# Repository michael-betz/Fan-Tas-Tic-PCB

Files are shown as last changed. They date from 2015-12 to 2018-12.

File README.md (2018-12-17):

# Fan-Tas-Tic-PCB
Kicad files for the Fan-Tas-Tic pinball controller.
No tiny SMD components, can be easily assembled by hand.
Designed for the milling machine (2 sided but no real vias, using through hole components instead).

# Mainboard

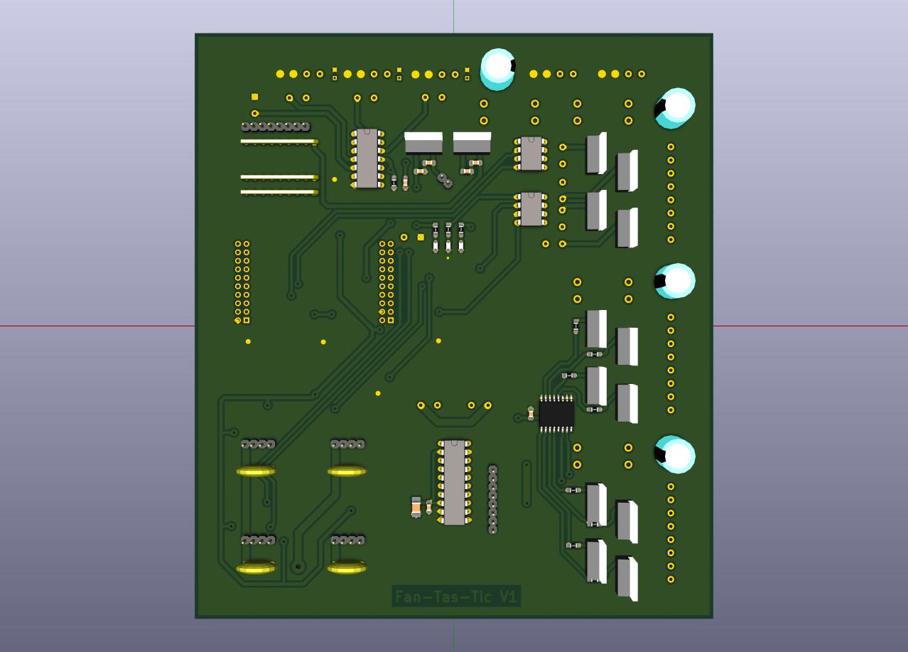
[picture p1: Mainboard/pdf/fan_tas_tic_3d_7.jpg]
3D view of the Mainboard


[Schematic](https://raw.githubusercontent.com/yetifrisstlama/Fan-Tas-Tic-PCB/master/Mainboard/pdf/fan_tas_tic.pdf)

 * Based on TM4C123GXL evaluation board
 * 8 x 8 Switch matrix inputs (Operating on 12 V)
 * 12 x on-board open drain drivers for solenoids
 * 4 of them can do hardware PWM (> 100 kHz)
 * Fused in groups of 4
 * 4 x I2C channels for hardware extension boards.
   In- / Outputs can be easily and cheaply added with PCF8574 I2C GPIO extenders
 * 3 x SPI channels for running WS2811 / WS2812 LED strings.
   Up to 1024 LEDs / channel.
 * USB virtual serial connection to host PC (or Raspberry PI)
 * 5 V can come from USB or from external 24 V input (Set JP1)
 * SMD resistors / capacitors = 0805
 * Switch matrix driver:
   [TPIC6B595](http://www.ti.com/lit/ds/symlink/tpic6b595.pdf) (eBay)
 * GPIO extender:
   [PCF8574](http://www.ti.com/lit/ds/symlink/pcf8574.pdf) (eBay)
 * Dual power mosfet driver:
   [UCC27524](http://www.ti.com/lit/ds/symlink/ucc27524.pdf)
 * Power mosfets:
   [IRL640](http://www.vishay.com/docs/91305/91305.pdf)
 * Signal mosfet for I2C level conversion:
   [BSS138](https://www.fairchildsemi.com/datasheets/BS/BSS138.pdf)
 * 8 pin solenoid and 4 pin power connectors:
   [HT396](https://www.google.com/search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,ssl&ei=fLGbVpy5GMX4apzWrtgK)
 * 8 pin switch-matrix and 4 pin I2C connectors:
   [KF2510](https://www.google.com/search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,ssl&ei=HrKbVpHDFoKua7iAu-AK)

## Status
The current version of the Mainboard PCB (06/2016) has been tested and worked as expected without any major problems. See also the [development blog](http://yetifrisstlama.blogspot.fr/). For the next revision, these (minor) issues will be fixed:
 * `Debug` USB connector on the Tiva board interferes with the I2C connectors on the mainboard. These will be moved.
 * An `Interlock` Relay will be introduced on the 24 V supply line for the solenoid drivers. This is needed as the I2C port extenders have by default all outputs active before beeing initialized (which only happens a few 10 ms after power up). Furthermore, if the firmware crashes, has I2C connection issues or locks up, it can cut the power from an fault-handler.
 * Freewheeling diodes _MUST_ be Schottky diodes and will be included on the PCB next to the mosfets (not on the solenoids!) for accetable EMI performance. This has been found experimentally (http://yetifrisstlama.blogspot.fr/).
 * More footprints for decoupling caps will be included

# Input extension board
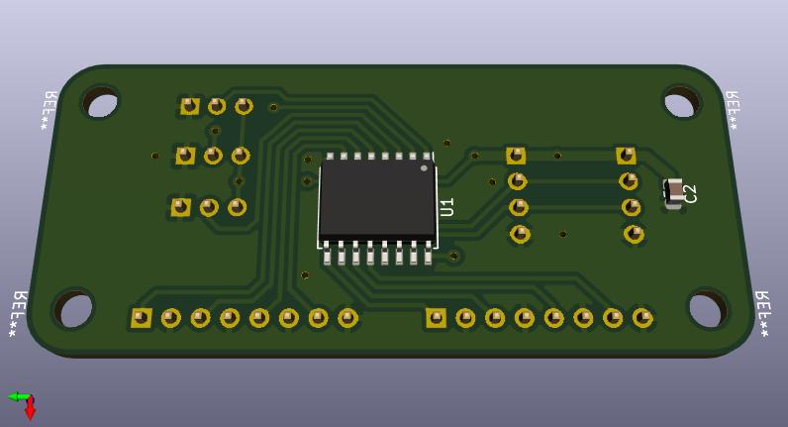
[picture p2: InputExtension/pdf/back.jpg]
3D view of the input extension board


[Schematic](https://raw.githubusercontent.com/yetifrisstlama/Fan-Tas-Tic-PCB/master/InputExtension/pdf/InputExtension.pdf)

 * 8 shiny new input channels for your pinball machine
 * as simple and cheap as it gets
 * read out a zooming 1000 times a second

## Status
[Built, tested, works as expected :)](https://yetifrisstlama.github.io/fan-tas-tic-score-reels/)

# Output extension board
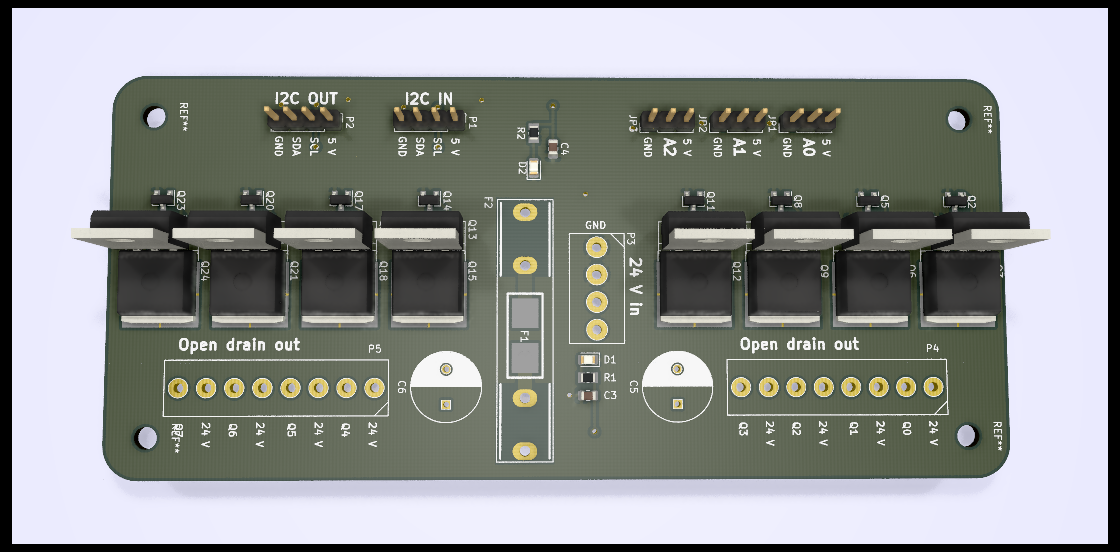
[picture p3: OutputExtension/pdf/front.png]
3D view of the output extension board


[Schematic](https://raw.githubusercontent.com/yetifrisstlama/Fan-Tas-Tic-PCB/master/OutputExtension/pdf/OutputExtension.pdf)

 * 8 beefy open drain outputs to rock some solenoids
 * BYOM! Bring your own mosfets ... supports TO-220, TO-263 and SOT23 footprints
 * Fused, to keep the magic smoke in
 * Also drives motors, LED strings, LED floodlights ...

## Status
Built, tested, no issues found. Drives my score reels like a charm.

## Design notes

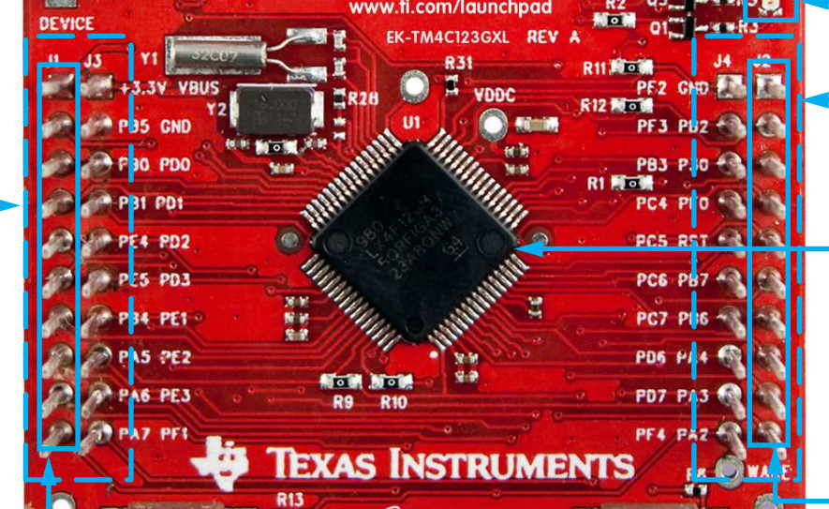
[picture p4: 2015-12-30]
Mainboard/TIVIA_Board.jpg

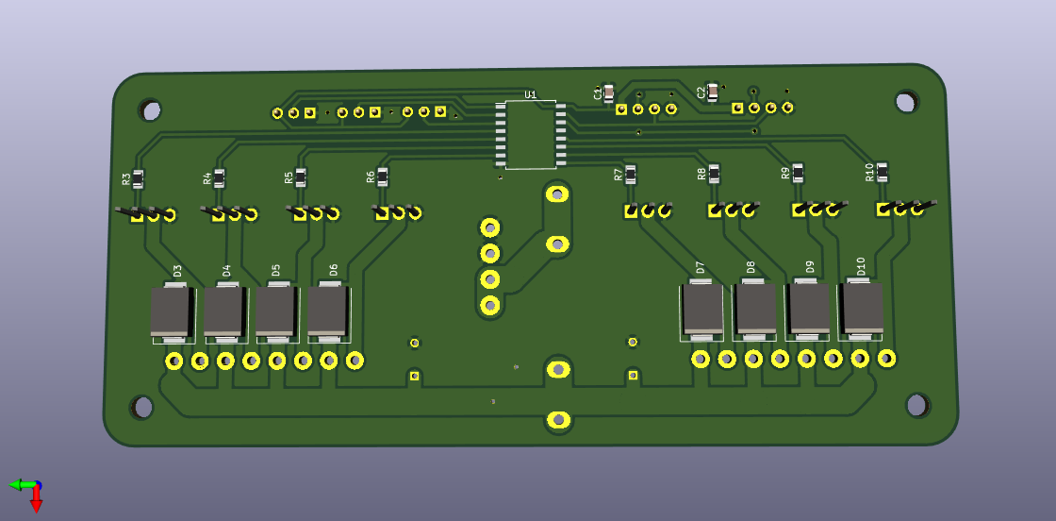
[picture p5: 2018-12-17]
OutputExtension/pdf/back.png

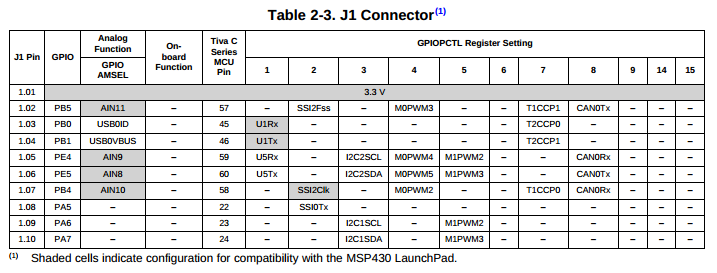
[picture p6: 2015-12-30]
Mainboard/TivaJ1.png

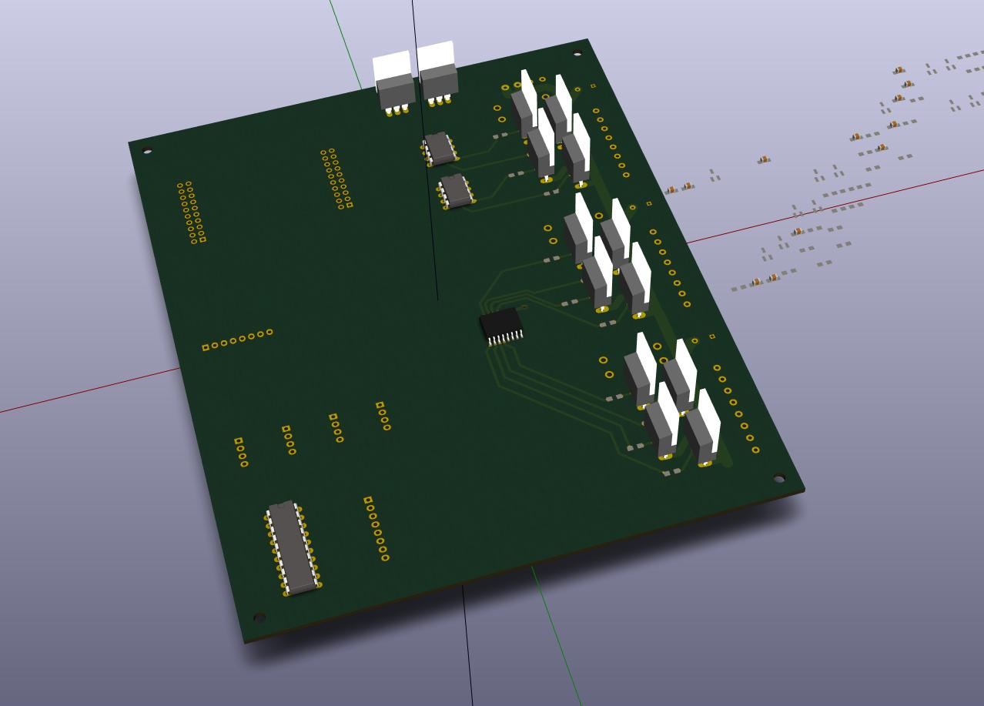
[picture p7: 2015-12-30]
Mainboard/pdf/fan_tas_tic_3d_2.jpg

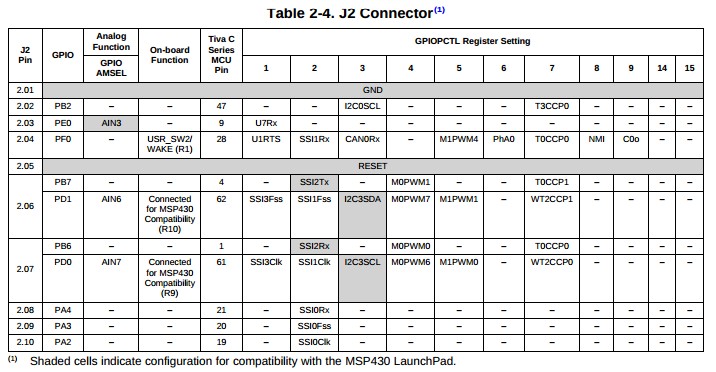
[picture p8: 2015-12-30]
Mainboard/TivaJ2.png

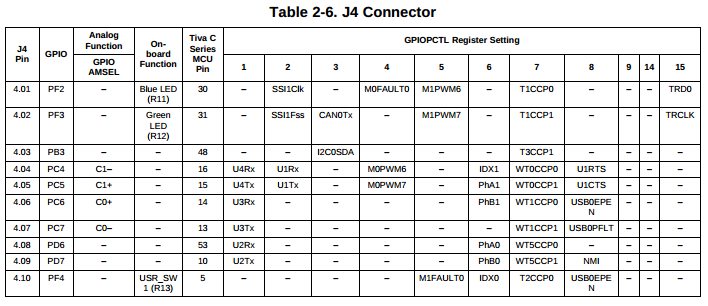
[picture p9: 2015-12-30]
Mainboard/TivaJ4.png

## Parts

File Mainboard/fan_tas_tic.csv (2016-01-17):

Reference | Value | Footprint | Datasheet
P6 | CONN_01X08 | Pin_Headers:Pin_Header_Straight_1x08
P8 | CONN_01X08 | Pin_Headers:Pin_Header_Straight_1x08
P7 | CONN_01X08 | my_foots:HT396_8
F1 | FUSE | Fuse_Holders_and_Fuses:Fuseholder5x20_horiz_open_universal_Type-III
C12 | 470 uF | Capacitors_ThroughHole:C_Radial_D10_L16_P5
U3 | UCC27524 | Housings_DIP:DIP-8_W7.62mm_LongPads
U4 | UCC27524 | Housings_DIP:DIP-8_W7.62mm_LongPads
C9 | 300nF | Capacitors_SMD:C_1812_HandSoldering
C10 | 300nF | Capacitors_SMD:C_1812_HandSoldering
R2 | 47R | Resistors_ThroughHole:Resistor_Vertical_RM5mm
R1 | 47R | Resistors_ThroughHole:Resistor_Vertical_RM5mm
R5 | 47R | Resistors_ThroughHole:Resistor_Vertical_RM5mm
R14 | 47R | Resistors_ThroughHole:Resistor_Vertical_RM5mm
C1 | 330n | Capacitors_SMD:C_0805_HandSoldering
C3 | 100n | Capacitors_SMD:C_0805_HandSoldering
P1 | CONN_01X04 | my_foots:HT396_4
C2 | 330n | Capacitors_SMD:C_0805_HandSoldering
P9 | CONN_01X08 | my_foots:HT396_8
F2 | FUSE | Fuse_Holders_and_Fuses:Fuseholder5x20_horiz_open_universal_Type-III
C14 | 470 uF | Capacitors_ThroughHole:C_Radial_D10_L16_P5
P10 | CONN_01X08 | my_foots:HT396_8
F3 | FUSE | Fuse_Holders_and_Fuses:Fuseholder5x20_horiz_open_universal_Type-III
C15 | 470 uF | Capacitors_ThroughHole:C_Radial_D10_L16_P5
U6 | PCF8574 | Housings_SOIC:SOIC-16_7.5x10.3mm_Pitch1.27mm
C13 | 100n | Capacitors_SMD:C_0805_HandSoldering
P2 | CONN_01X04 | Pin_Headers:Pin_Header_Straight_1x04
C5 | 100n | Capacitors_ThroughHole:C_Disc_D12_P7.75
P3 | CONN_01X04 | Pin_Headers:Pin_Header_Straight_1x04
C6 | 100n | Capacitors_ThroughHole:C_Disc_D12_P7.75
P4 | CONN_01X04 | Pin_Headers:Pin_Header_Straight_1x04
C7 | 100n | Capacitors_ThroughHole:C_Disc_D12_P7.75
P5 | CONN_01X04 | Pin_Headers:Pin_Header_Straight_1x04
C8 | 100n | Capacitors_ThroughHole:C_Disc_D12_P7.75
R6 | 30k | Resistors_SMD:R_0805_HandSoldering
R7 | 30k | Resistors_SMD:R_0805_HandSoldering
R8 | 30k | Resistors_SMD:R_0805_HandSoldering
R9 | 30k | Resistors_SMD:R_0805_HandSoldering
R10 | 30k | Resistors_SMD:R_0805_HandSoldering
R11 | 30k | Resistors_SMD:R_0805_HandSoldering
R12 | 30k | Resistors_SMD:R_0805_HandSoldering
R13 | 30k | Resistors_SMD:R_0805_HandSoldering
C11 | 100n | Capacitors_SMD:C_0805_HandSoldering
R3 | 30k | Resistors_ThroughHole:Resistor_Vertical_RM5mm
R4 | 30k | Resistors_ThroughHole:Resistor_Vertical_RM5mm
U5 | TPIC6B595 | Housings_DIP:DIP-20_W7.62mm_LongPads
Q1 | IRL640 | TO_SOT_Packages_THT:TO-220_Neutral123_Vertical_LargePads
Q2 | IRL640 | TO_SOT_Packages_THT:TO-220_Neutral123_Vertical_LargePads
Q3 | IRL640 | TO_SOT_Packages_THT:TO-220_Neutral123_Vertical_LargePads
Q4 | IRL640 | TO_SOT_Packages_THT:TO-220_Neutral123_Vertical_LargePads
U2 | 7805 | my_foots:TO-220_Neutral123_Vertical_LargePads
U1 | 7812 | my_foots:TO-220_Neutral123_Vertical_LargePads
JP1 | Jumper_NO_Small | Pin_Headers:Pin_Header_Straight_1x02
C4 | 100n | Capacitors_SMD:C_0805_HandSoldering
P11 | CONN_01X04 | my_foots:HT396_4
C16 | 4700 uF | Capacitors_ThroughHole:C_Radial_D10_L16_P5
F4 | 10A | Fuse_Holders_and_Fuses:Fuseholder5x20_horiz_open_universal_Type-III
P13 | CONN_01X04 | my_foots:HT396_4
R51 | 470 | Resistors_ThroughHole:Resistor_Vertical_RM5mm
C18 | 300 nF | Capacitors_ThroughHole:C_Rect_L4_W2.5_P2.5
RR1 | RR8 | Resistors_ThroughHole:Resistor_Array_SIP8
RR2 | RR8 | Resistors_ThroughHole:Resistor_Array_SIP8
RR3 | RR8 | Resistors_ThroughHole:Resistor_Array_SIP8
C19 | 10u | Capacitors_SMD:C_1210_HandSoldering
P14 | CONN_01X04 | my_foots:HT396_4
R22 | 470 | Resistors_ThroughHole:Resistor_Vertical_RM5mm
C20 | 300 nF | Capacitors_ThroughHole:C_Rect_L4_W2.5_P2.5
P12 | CONN_01X04 | my_foots:HT396_4
R20 | 470 | Resistors_ThroughHole:Resistor_Vertical_RM5mm
C17 | 300 nF | Capacitors_ThroughHole:C_Rect_L4_W2.5_P2.5
C21 | 470n | Capacitors_SMD:C_0805_HandSoldering
C22 | 470n | Capacitors_SMD:C_0805_HandSoldering
D3 | LED | LEDs:LED-0805
R17 | 220 | Resistors_SMD:R_0805_HandSoldering
D2 | LED | LEDs:LED-0805
R16 | 820 | Resistors_SMD:R_0805_HandSoldering
D1 | LED | LEDs:LED-0805
R15 | 2200 | Resistors_SMD:R_0805_HandSoldering
U7 | 74HC04 | Housings_DIP:DIP-14_W7.62mm_LongPads
R18 | 4k7 | Resistors_ThroughHole:Resistor_Vertical_RM5mm
R19 | 4k7 | Resistors_ThroughHole:Resistor_Vertical_RM5mm
R21 | 4k7 | Resistors_SMD:R_0805_HandSoldering
C23 | 100nF | Capacitors_SMD:C_0805_HandSoldering
J1 | Ti_Booster_40 | my_foots:Tivia_Launch_Pad
R23 | 470R | Resistors_SMD:R_0805_HandSoldering
Q5 | IRL640 | TO_SOT_Packages_THT:TO-220_Neutral123_Vertical_LargePads
R24 | 470R | Resistors_SMD:R_0805_HandSoldering
Q6 | IRL640 | TO_SOT_Packages_THT:TO-220_Neutral123_Vertical_LargePads
R25 | 470R | Resistors_SMD:R_0805_HandSoldering
Q7 | IRL640 | TO_SOT_Packages_THT:TO-220_Neutral123_Vertical_LargePads
R26 | 470R | Resistors_SMD:R_0805_HandSoldering
Q8 | IRL640 | TO_SOT_Packages_THT:TO-220_Neutral123_Vertical_LargePads
R27 | 470R | Resistors_SMD:R_0805_HandSoldering
Q9 | IRL640 | TO_SOT_Packages_THT:TO-220_Neutral123_Vertical_LargePads
R28 | 470R | Resistors_SMD:R_0805_HandSoldering
Q10 | IRL640 | TO_SOT_Packages_THT:TO-220_Neutral123_Vertical_LargePads
R29 | 470R | Resistors_SMD:R_0805_HandSoldering
Q11 | IRL640 | TO_SOT_Packages_THT:TO-220_Neutral123_Vertical_LargePads
R30 | 470R | Resistors_SMD:R_0805_HandSoldering
Q12 | IRL640 | TO_SOT_Packages_THT:TO-220_Neutral123_Vertical_LargePads
R31 | 2k2 | Resistors_SMD:R_0805_HandSoldering
R32 | 2k2 | Resistors_SMD:R_0805_HandSoldering
R33 | 2k2 | Resistors_SMD:R_0805_HandSoldering
R34 | 2k2 | Resistors_SMD:R_0805_HandSoldering
Q13 | BSS138 | TO_SOT_Packages_SMD:SOT-23_Handsoldering
Q14 | BSS138 | TO_SOT_Packages_SMD:SOT-23_Handsoldering
R35 | 2k2 | Resistors_SMD:R_0805_HandSoldering
R36 | 2k2 | Resistors_SMD:R_0805_HandSoldering
R37 | 2k2 | Resistors_SMD:R_0805_HandSoldering
R38 | 2k2 | Resistors_SMD:R_0805_HandSoldering
Q15 | BSS138 | TO_SOT_Packages_SMD:SOT-23_Handsoldering
Q16 | BSS138 | TO_SOT_Packages_SMD:SOT-23_Handsoldering
R39 | 2k2 | Resistors_SMD:R_0805_HandSoldering
R40 | 2k2 | Resistors_SMD:R_0805_HandSoldering
R41 | 2k2 | Resistors_SMD:R_0805_HandSoldering
R42 | 2k2 | Resistors_SMD:R_0805_HandSoldering
Q17 | BSS138 | TO_SOT_Packages_SMD:SOT-23_Handsoldering
Q18 | BSS138 | TO_SOT_Packages_SMD:SOT-23_Handsoldering
R43 | 2k2 | Resistors_SMD:R_0805_HandSoldering
R44 | 2k2 | Resistors_SMD:R_0805_HandSoldering
R45 | 2k2 | Resistors_SMD:R_0805_HandSoldering
R46 | 2k2 | Resistors_SMD:R_0805_HandSoldering
Q19 | BSS138 | TO_SOT_Packages_SMD:SOT-23_Handsoldering
Q20 | BSS138 | TO_SOT_Packages_SMD:SOT-23_Handsoldering

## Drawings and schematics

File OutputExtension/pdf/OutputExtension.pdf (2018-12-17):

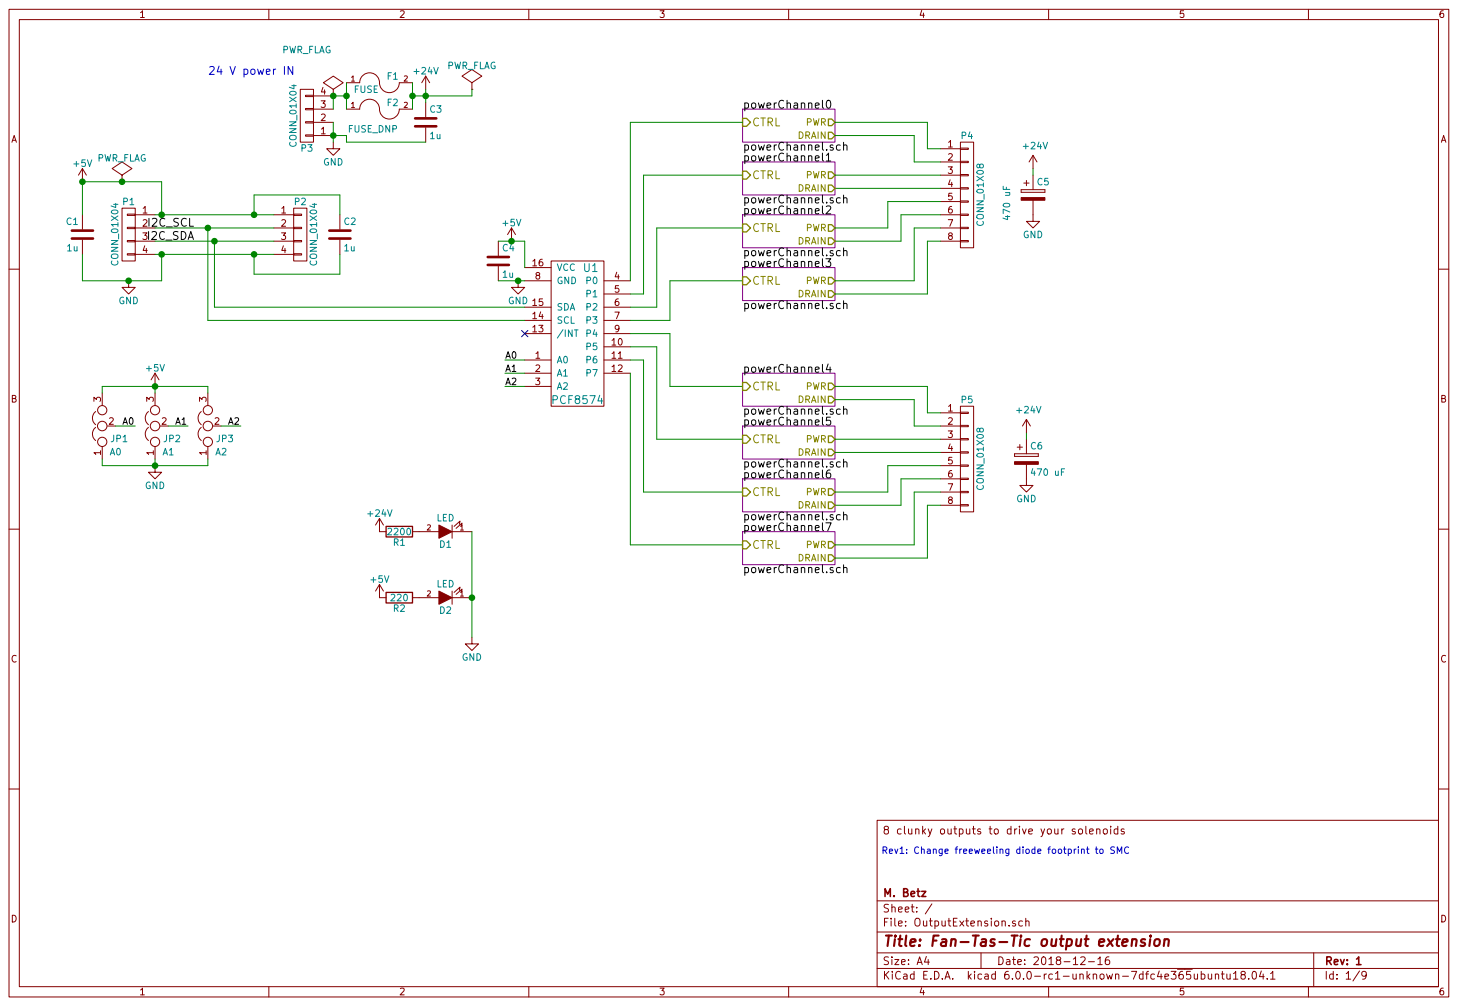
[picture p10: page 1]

File: OutputExtension.sch Sheet: / M. Betz 8 clunky outputs to drive your solenoids

Rev1: Change freeweeling diode footprint to SMC

Id: 1/9 Title: Fan-Tas-Tic output extension

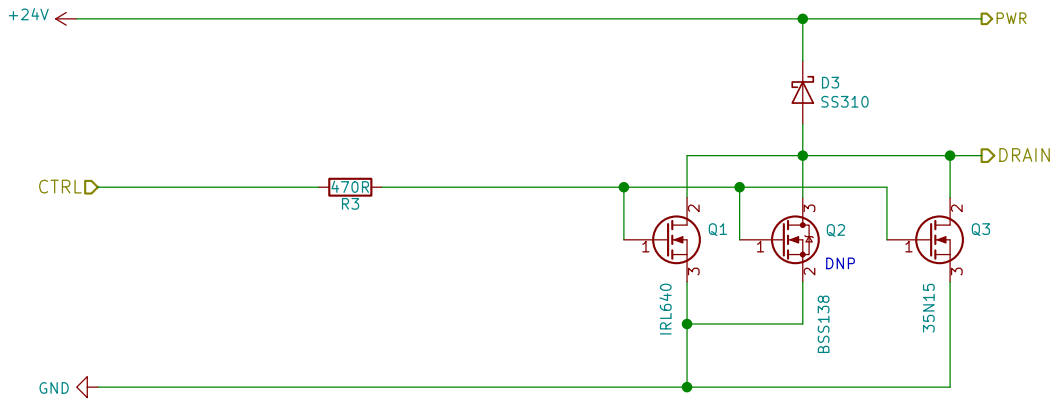
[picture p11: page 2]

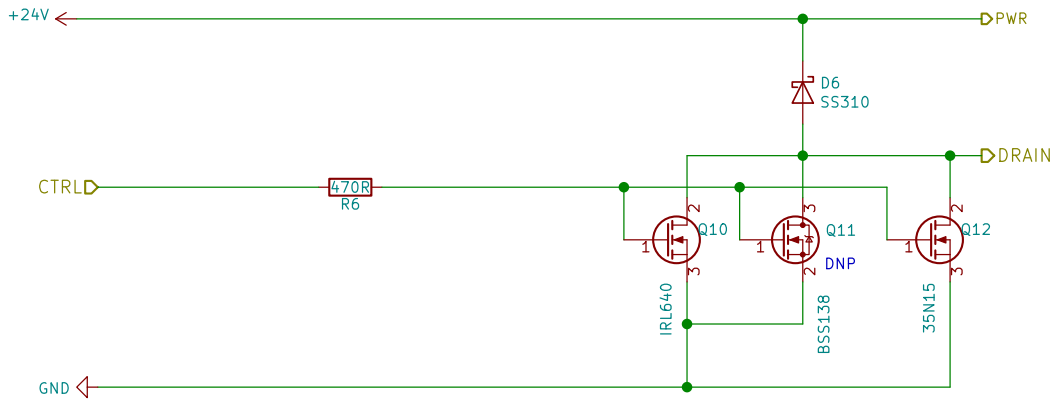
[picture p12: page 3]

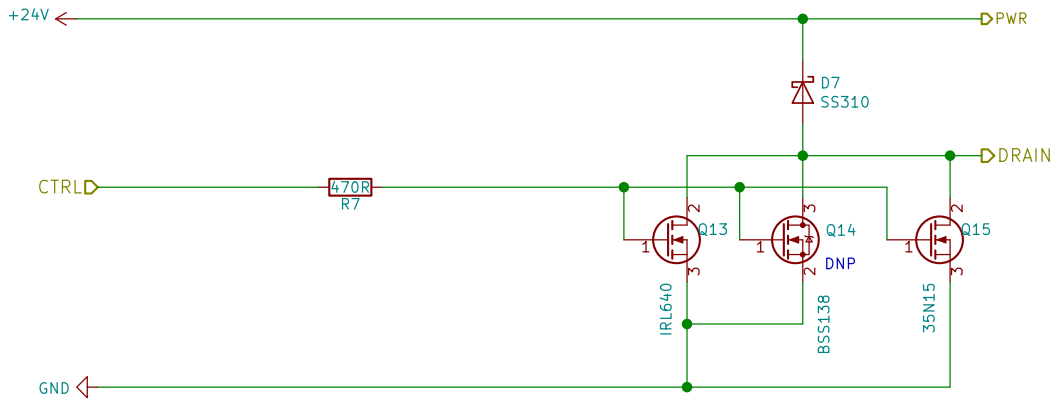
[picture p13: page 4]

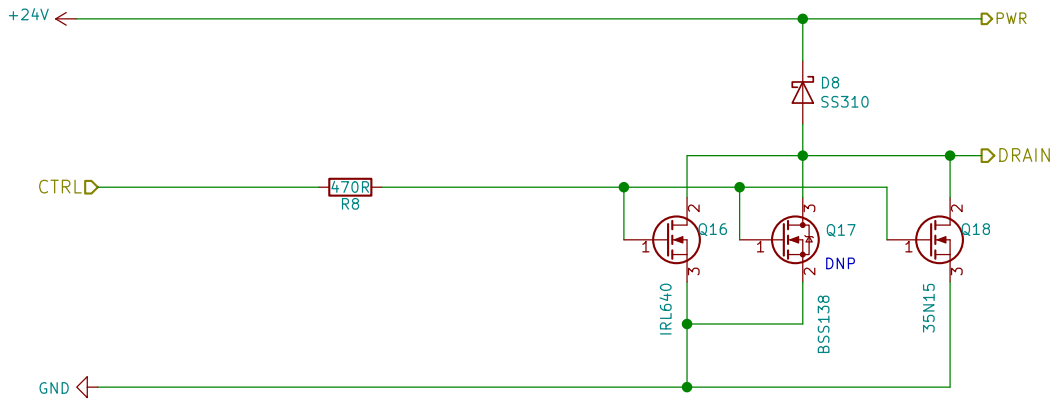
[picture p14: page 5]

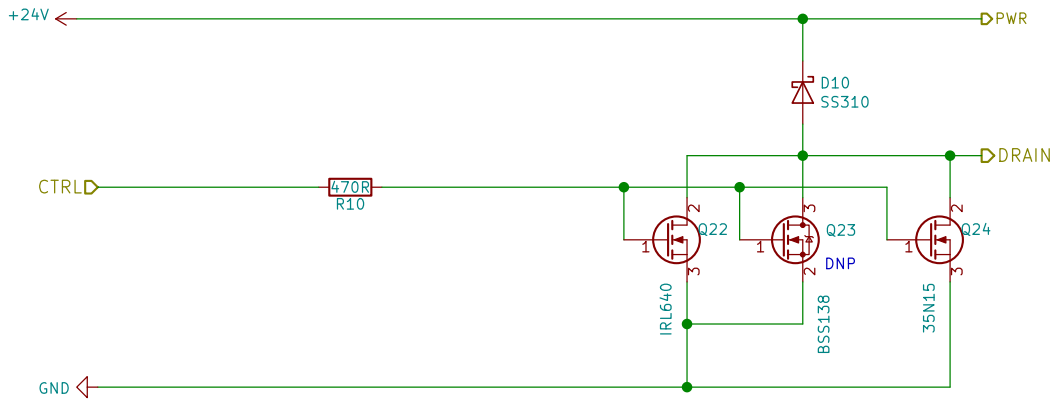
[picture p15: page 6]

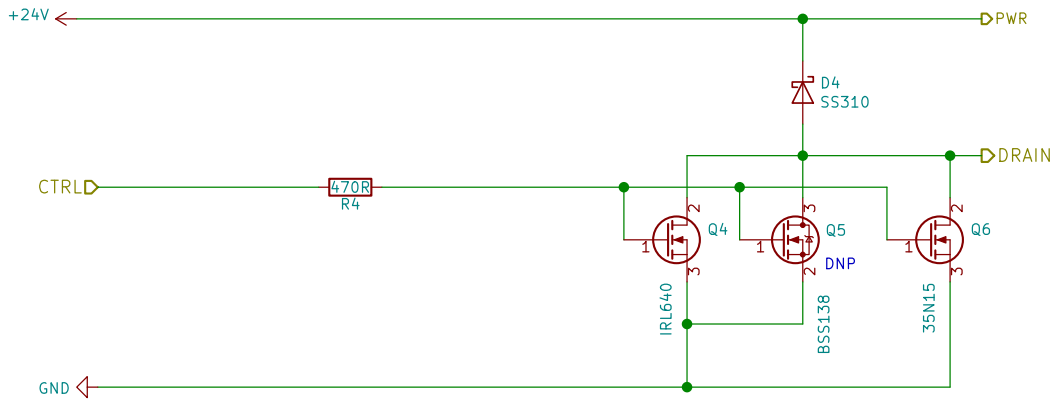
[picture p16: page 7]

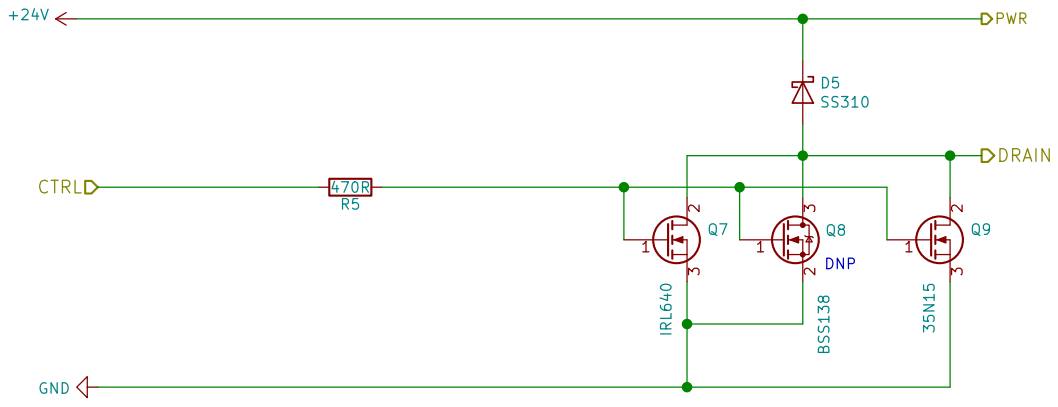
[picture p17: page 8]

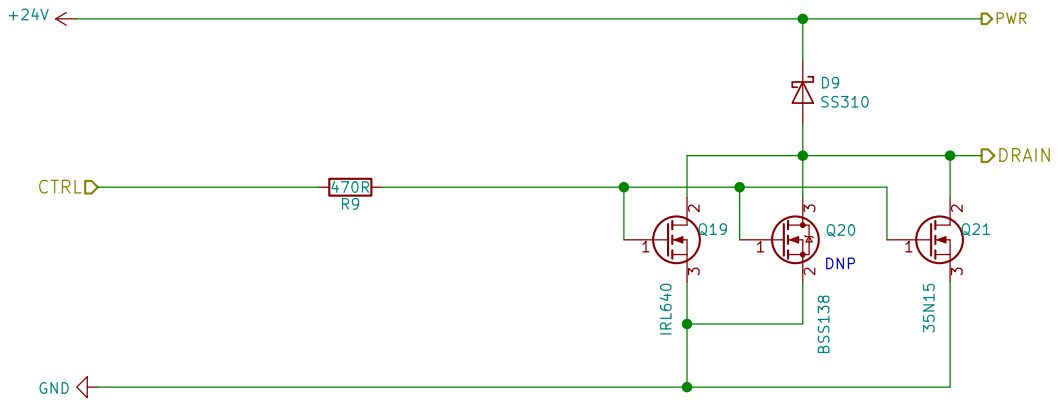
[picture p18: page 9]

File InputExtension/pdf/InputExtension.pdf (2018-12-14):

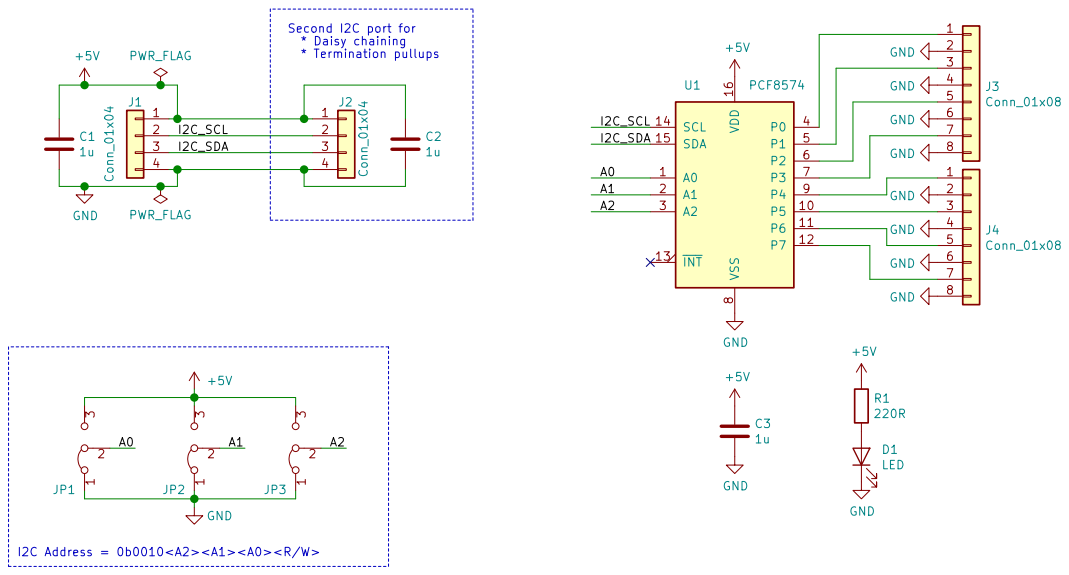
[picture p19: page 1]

J4Conn_01x08 GND GND GND GND GND GND GND GND

File: InputExtension.sch Sheet: / M. Betz 8 shiny new inputs for your pinball machine

Id: 1/1 Title: Fan-Tas-Tic input extension

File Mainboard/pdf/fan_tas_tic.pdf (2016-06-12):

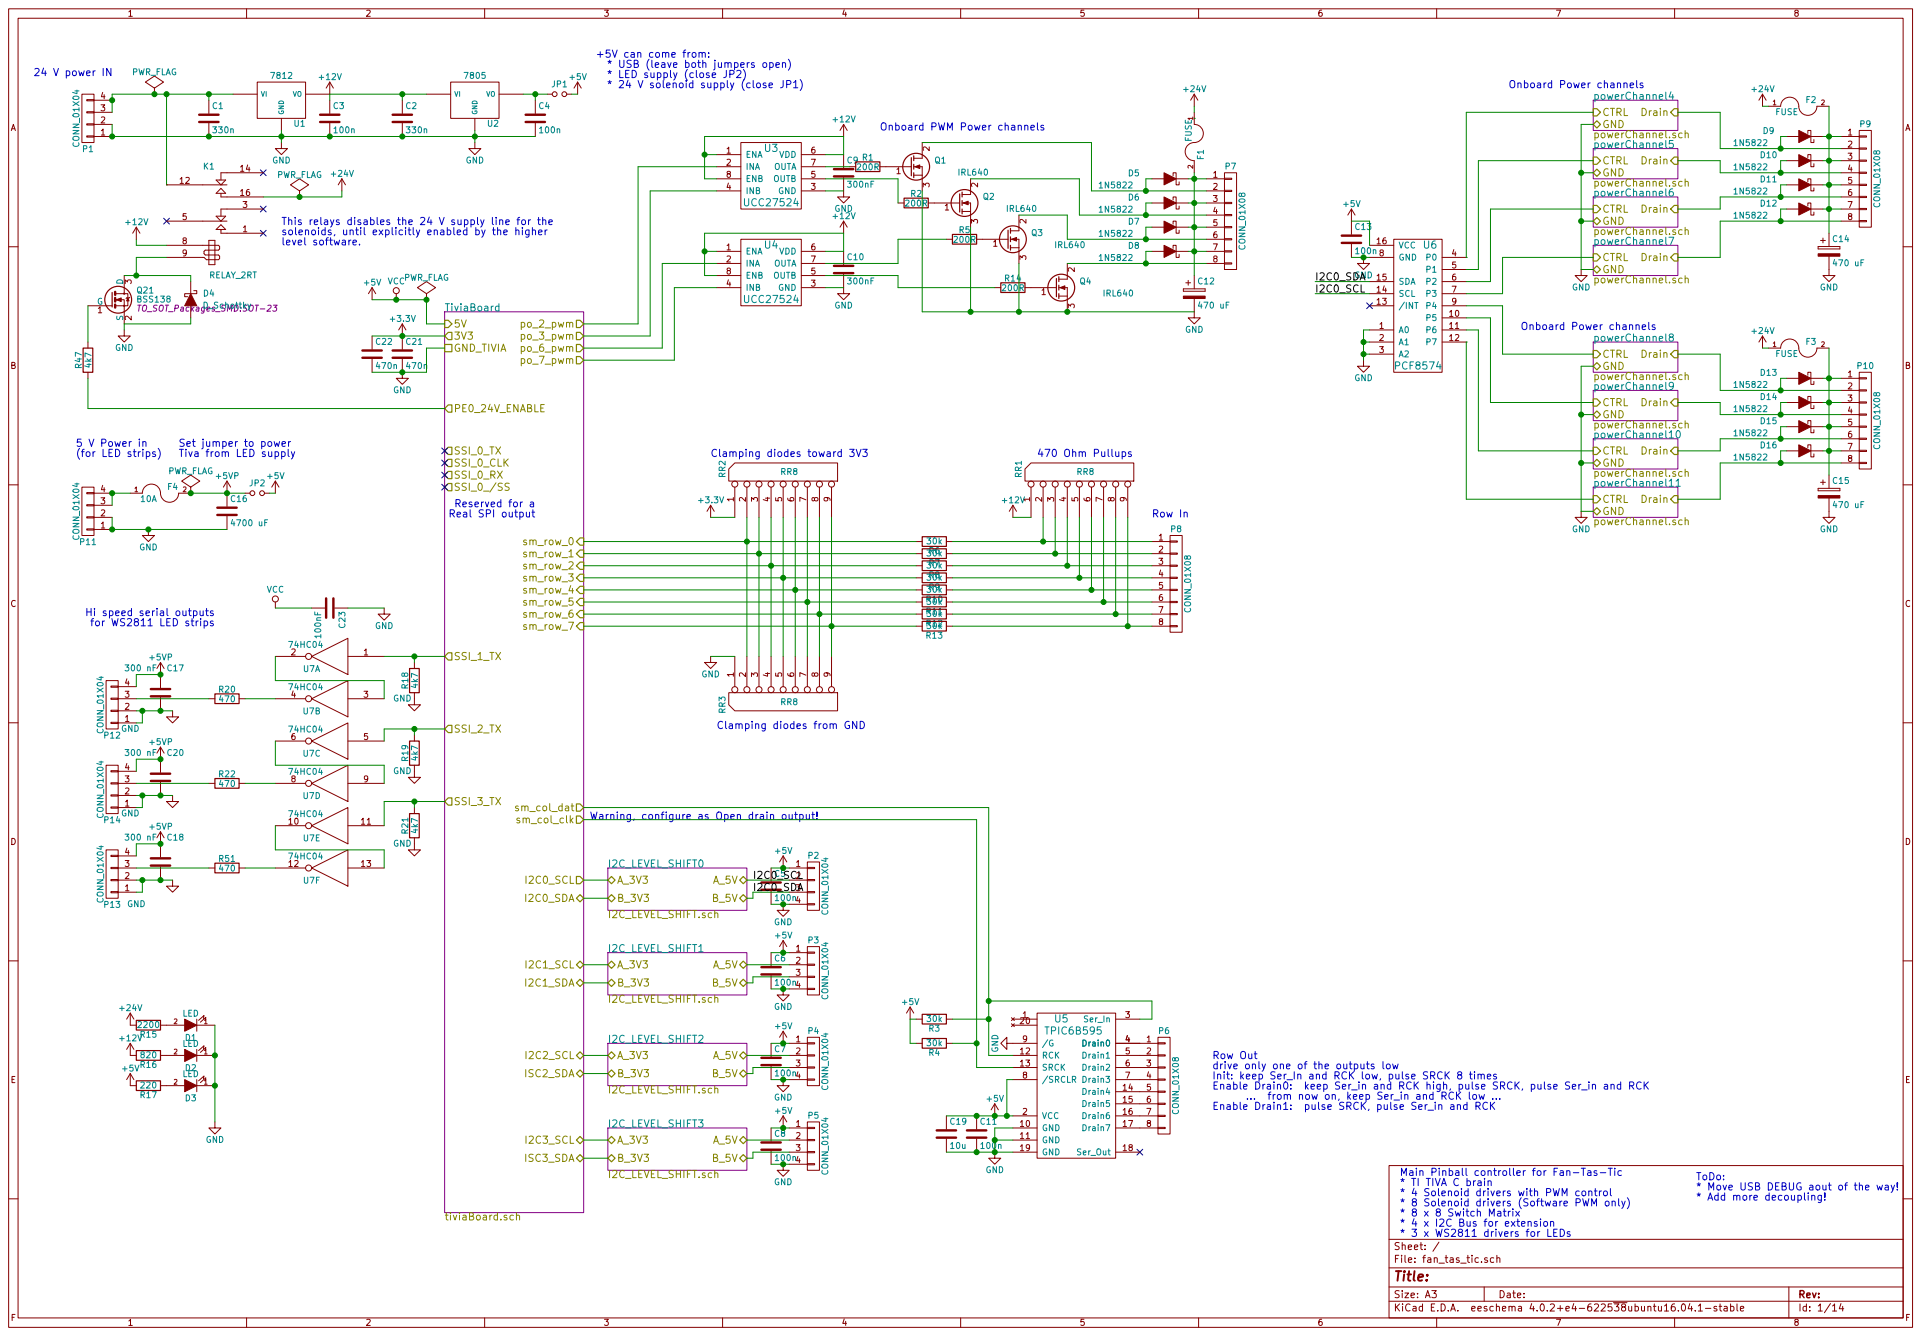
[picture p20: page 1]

* USB (leave both jumpers open)
* LED supply (close JP2)

Onboard Power channels
+24V GND Onboard Power channels

Onboard PWM Power channels

This relays disables the 24 V supply line for the
solenoids, until explicitly enabled by the higher

JP2 +5V Set jumper to power
Tiva from LED supply
PWR_FLAG

9 RR3RR8 GNDClamping diodes toward 3V3 470 Ohm Pullups

Clamping diodes from GND

Row Out
drive only one of the outputs low
Init: keep Ser_In and RCK low, pulse SRCK 8 times
Enable Drain0: keep Ser_in and RCK high, pulse SRCK, pulse Ser_in and RCK
... from now on, keep Ser_in and RCK low ...
Enable Drain1: pulse SRCK, pulse Ser_in and RCK

/SRCLR 8 | 4

Main Pinball controller for Fan-Tas-Tic
* TI TIVA C brain
* 4 Solenoid drivers with PWM control
* 8 Solenoid drivers (Software PWM only)
* 8 x 8 Switch Matrix
* 4 x I2C Bus for extension
* 3 x WS2811 drivers for LEDs
File: fan_tas_tic.sch Sheet: /

ToDo: * Move USB DEBUG aout of the way!
* Add more decoupling!

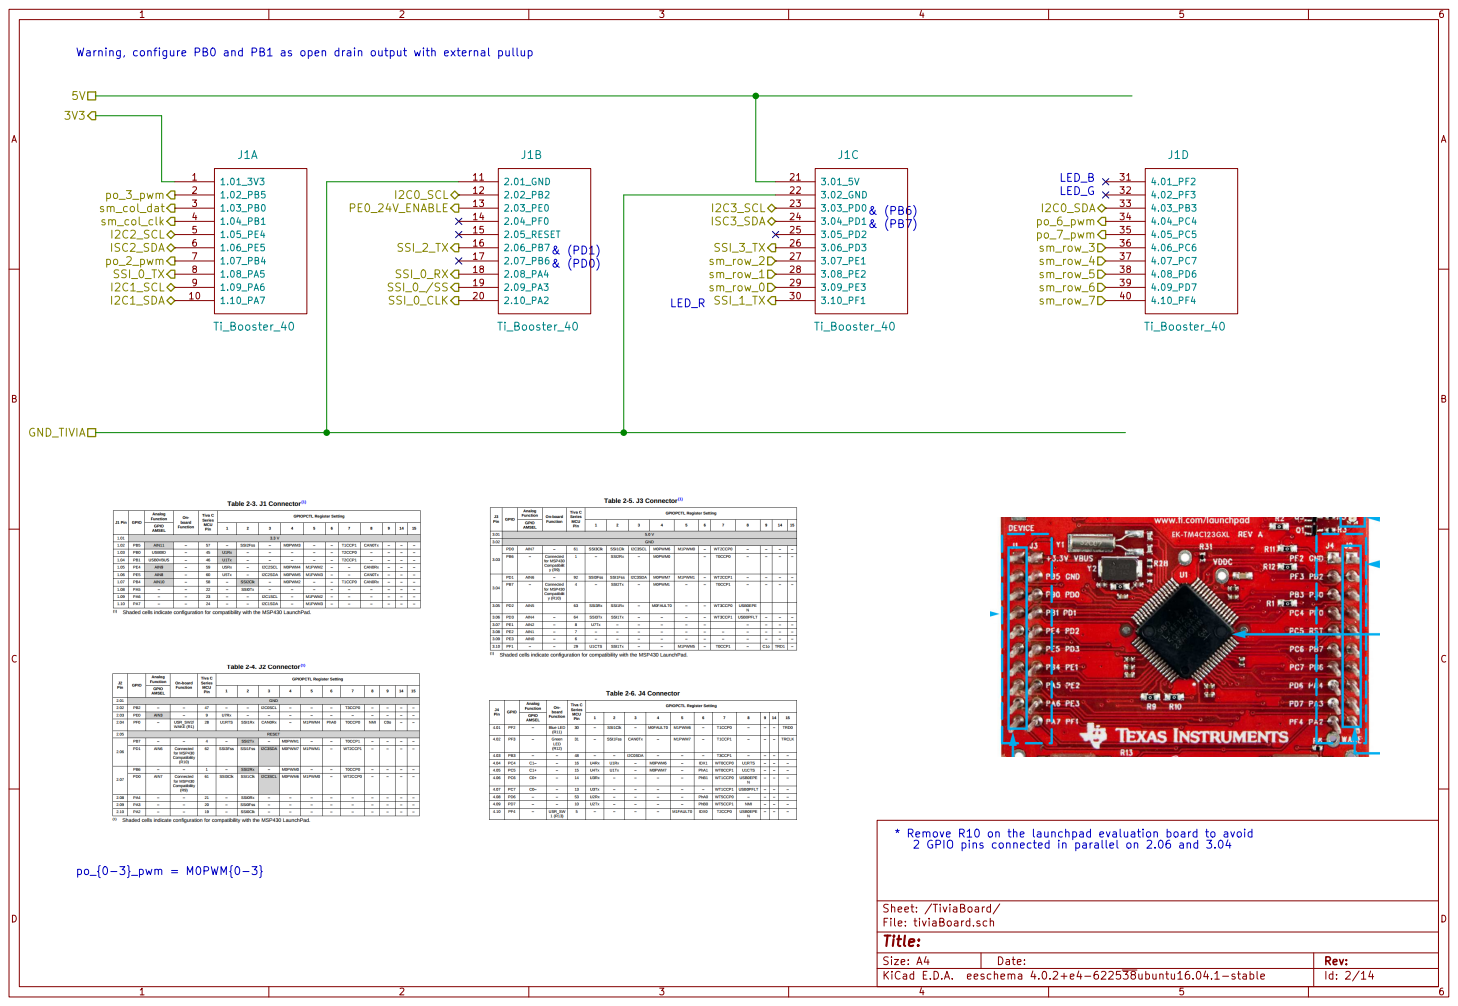
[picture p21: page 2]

Warning, configure PB0 and PB1 as open drain output with external pullup

* Remove R10 on the launchpad evaluation board to avoid
2 GPIO pins connected in parallel on 2.06 and 3.04

Id: 2/14 Title: File: tiviaBoard.sch Sheet: /TiviaBoard/

















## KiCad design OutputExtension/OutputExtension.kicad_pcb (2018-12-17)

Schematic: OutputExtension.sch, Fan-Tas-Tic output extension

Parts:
C1, C2, C3, C4: 1u; C_0805_2012Metric
C5, C6: 470 uF; C_Radial_D10_L16_P5
D1, D2: LED; LED_0805_2012Metric
F1: FUSE; LBL_FUSE
F2: FUSE_DNP; littlefuse_154_smd
JP1: A0; PinHeader_1x03_P2.54mm_Vertical
JP2: A1; PinHeader_1x03_P2.54mm_Vertical
JP3: A2; PinHeader_1x03_P2.54mm_Vertical
P1, P2: CONN_01X04; PinHeader_1x04_P2.54mm_Vertical
P3: CONN_01X04; HT396_4
P4, P5: CONN_01X08; HT396_8
R1: 2200; R_0805_2012Metric
R2: 220; R_0805_2012Metric
U1: PCF8574; SOIC-16_7.5x10.3mm_Pitch1.27mm

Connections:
+5V: C1.1, C2.1, C4.1, JP1.3, JP2.3, JP3.3, P1.1, P2.1, R2.2, U1.16 (VCC)
+24V: C3.1, C5.1, C6.1, F1.2, F2.2, P4.1, P4.3, P4.5, P4.7, P5.1, P5.3, P5.5, P5.7, R1.2; also elsewhere on the board
/A0: JP1.2, U1.1 (A0)
/A1: JP2.2, U1.2 (A1)
/A2: JP3.2, U1.3 (A2)
/I2C_SCL: P1.2, P2.2, U1.14 (SCL)
/I2C_SDA: P1.3, P2.3, U1.15 (SDA)
/powerChannel0/CTRL: U1.4 (P0); also elsewhere on the board
/powerChannel0/DRAIN: P4.2; also elsewhere on the board
/powerChannel1/CTRL: U1.5 (P1); also elsewhere on the board
/powerChannel1/DRAIN: P4.4; also elsewhere on the board
/powerChannel2/CTRL: U1.6 (P2); also elsewhere on the board
/powerChannel2/DRAIN: P4.6; also elsewhere on the board
/powerChannel3/CTRL: U1.7 (P3); also elsewhere on the board
/powerChannel3/DRAIN: P4.8; also elsewhere on the board
/powerChannel4/CTRL: U1.9 (P4); also elsewhere on the board
/powerChannel4/DRAIN: P5.2; also elsewhere on the board
/powerChannel5/CTRL: U1.10 (P5); also elsewhere on the board
/powerChannel5/DRAIN: P5.4; also elsewhere on the board
/powerChannel6/CTRL: U1.11 (P6); also elsewhere on the board
/powerChannel6/DRAIN: P5.6; also elsewhere on the board
/powerChannel7/CTRL: U1.12 (P7); also elsewhere on the board
/powerChannel7/DRAIN: P5.8; also elsewhere on the board
unnamed: D1.2 (A), R1.1
unnamed: D2.2 (A), R2.1
unnamed: F1.1, F2.1, P3.3, P3.4

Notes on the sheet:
24 V power IN
Rev1: Change freeweeling diode footprint to SMC

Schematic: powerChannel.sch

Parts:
D3: SS310; D_SMC
Q1: IRL640; TO-220-3_Vertical
Q2: BSS138; SOT-23
Q3: 35N15; TO-263-3_TabPin2
R3: 470R; R_0805_2012Metric

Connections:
+24V: D3.1; also elsewhere on the board
/powerChannel0/CTRL: R3.2; also elsewhere on the board
/powerChannel0/DRAIN: D3.2, Q1.2 (D), Q2.3, Q3.2 (D); also elsewhere on the board
unnamed: Q1.1 (G), Q2.1, Q3.1 (G), R3.1

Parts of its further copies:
D4, D5, D6, D7, D8, D9, D10: SS310; D_SMC
Q4, Q7, Q10, Q13, Q16, Q19, Q22: IRL640; TO-220-3_Vertical
Q5, Q8, Q11, Q14, Q17, Q20, Q23: BSS138; SOT-23
Q6, Q9, Q12, Q15, Q18, Q21, Q24: 35N15; TO-263-3_TabPin2
R4, R5, R6, R7, R8, R9, R10: 470R; R_0805_2012Metric

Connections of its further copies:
+24V: D4.1, D5.1, D6.1, D7.1, D8.1, D9.1, D10.1; also elsewhere on the board
/powerChannel1/CTRL: R4.2; also elsewhere on the board
/powerChannel1/DRAIN: D4.2, Q4.2 (D), Q5.3, Q6.2 (D); also elsewhere on the board
/powerChannel2/CTRL: R5.2; also elsewhere on the board
/powerChannel2/DRAIN: D5.2, Q7.2 (D), Q8.3, Q9.2 (D); also elsewhere on the board
/powerChannel3/CTRL: R6.2; also elsewhere on the board
/powerChannel3/DRAIN: D6.2, Q10.2 (D), Q11.3, Q12.2 (D); also elsewhere on the board
/powerChannel4/CTRL: R7.2; also elsewhere on the board
/powerChannel4/DRAIN: D7.2, Q13.2 (D), Q14.3, Q15.2 (D); also elsewhere on the board
/powerChannel5/CTRL: R8.2; also elsewhere on the board
/powerChannel5/DRAIN: D8.2, Q16.2 (D), Q17.3, Q18.2 (D); also elsewhere on the board
/powerChannel6/CTRL: R9.2; also elsewhere on the board
/powerChannel6/DRAIN: D9.2, Q19.2 (D), Q20.3, Q21.2 (D); also elsewhere on the board
/powerChannel7/CTRL: R10.2; also elsewhere on the board
/powerChannel7/DRAIN: D10.2, Q22.2 (D), Q23.3, Q24.2 (D); also elsewhere on the board
unnamed: Q4.1 (G), Q5.1, Q6.1 (G), R4.1
unnamed: Q7.1 (G), Q8.1, Q9.1 (G), R5.1
unnamed: Q10.1 (G), Q11.1, Q12.1 (G), R6.1
unnamed: Q13.1 (G), Q14.1, Q15.1 (G), R7.1
unnamed: Q16.1 (G), Q17.1, Q18.1 (G), R8.1
unnamed: Q19.1 (G), Q20.1, Q21.1 (G), R9.1
unnamed: Q22.1 (G), Q23.1, Q24.1 (G), R10.1

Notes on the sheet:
DNP

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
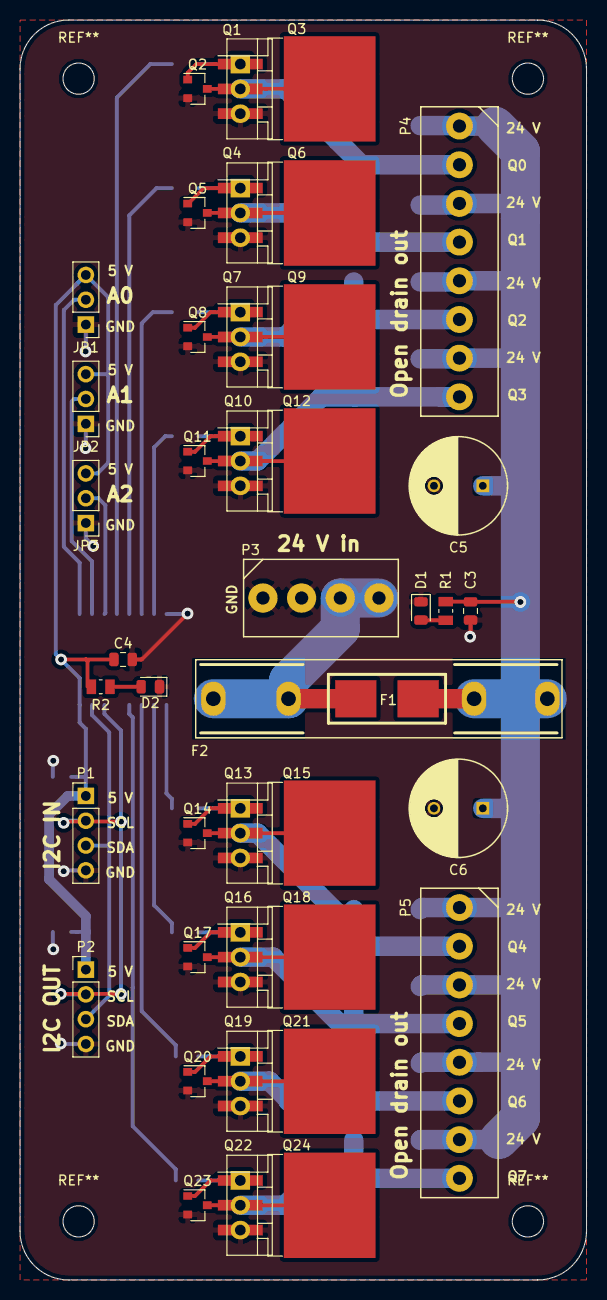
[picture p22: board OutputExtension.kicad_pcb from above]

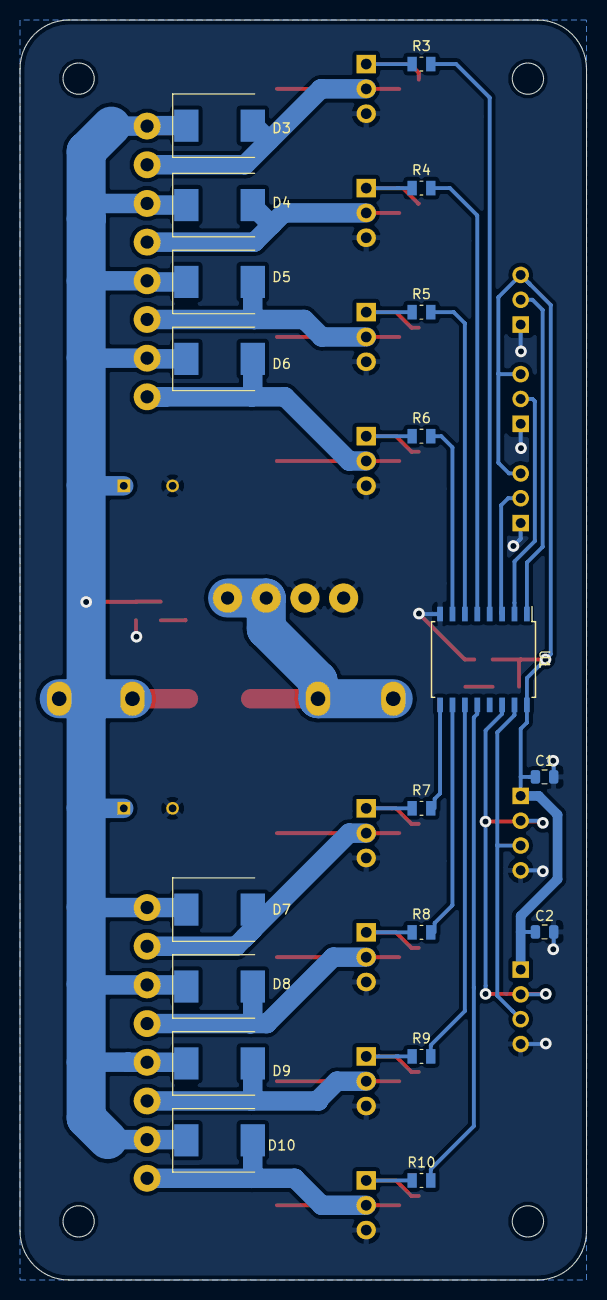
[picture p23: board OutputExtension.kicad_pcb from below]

Board: 2 copper layers, 58.0 x 129.0 mm, 61 parts (19 on the bottom side), 35 nets.

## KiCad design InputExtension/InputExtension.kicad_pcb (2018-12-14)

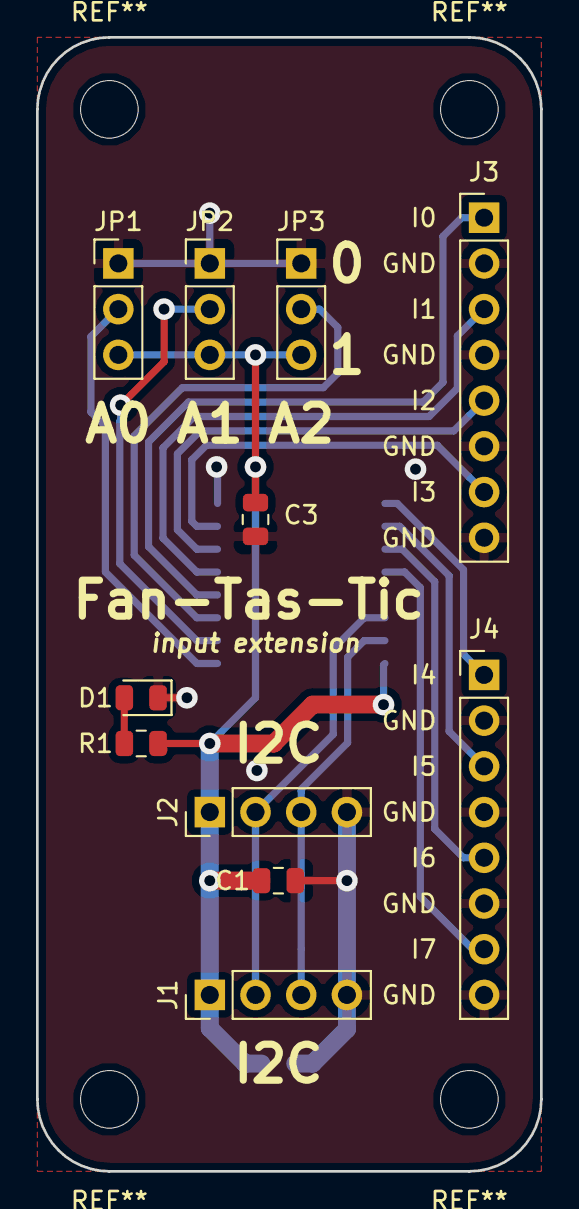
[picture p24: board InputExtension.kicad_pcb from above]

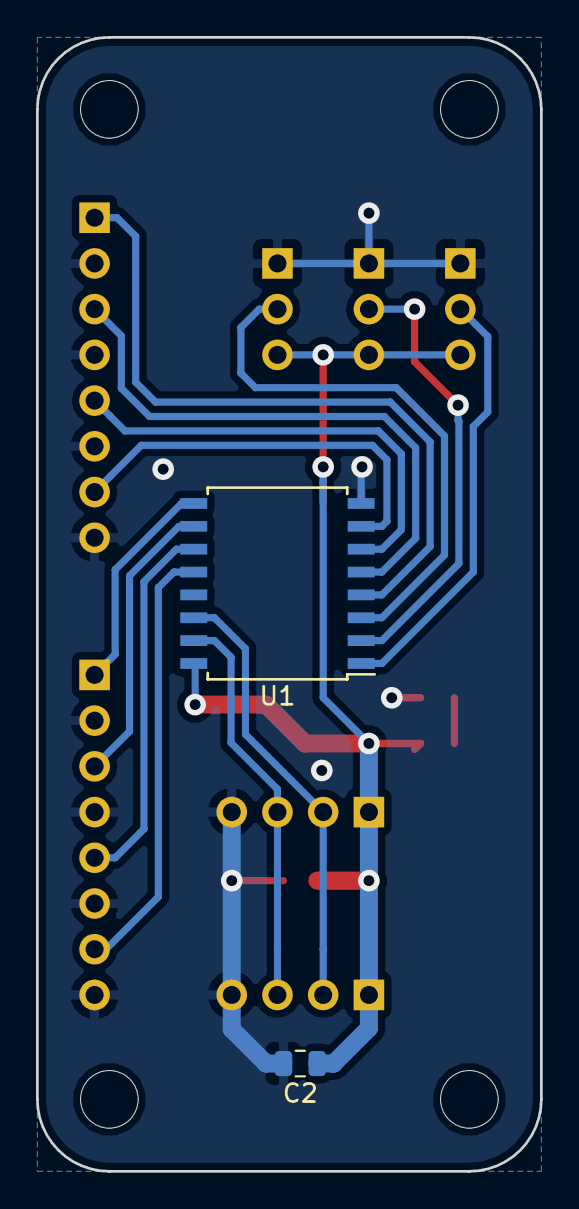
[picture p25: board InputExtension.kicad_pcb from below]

Board: 2 copper layers, 28.0 x 63.0 mm, 13 parts (2 on the bottom side), 16 nets.

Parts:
C1, C2, C3: 1u; C_0805_2012Metric
D1: LED; LED_0805_2012Metric
J1, J2: Conn_01x04; PinHeader_1x04_P2.54mm_Vertical
J3, J4: Conn_01x08; PinHeader_1x08_P2.54mm_Vertical
JP1, JP2, JP3: JP; PinHeader_1x03_P2.54mm_Vertical
R1: 220R; R_0805_2012Metric
U1: PCF8574; SOIC-16W_7.5x10.3mm_P1.27mm

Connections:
+5V: C1.1, C2.1, C3.1, J1.1, J2.1, JP1.3, JP2.3, JP3.3, R1.1, U1.16
/A0: JP1.2, U1.1
/A1: JP2.2, U1.2
/A2: JP3.2, U1.3
/I2C_SCL: J1.2, J2.2, U1.14
/I2C_SDA: J1.3, J2.3, U1.15
GND: C1.2, C2.2, C3.2, D1.1, J1.4, J2.4, J3.2, J3.4, J3.6, J3.8, J4.2, J4.4, J4.6, J4.8, JP1.1, JP2.1, JP3.1, U1.8
unnamed: D1.2, R1.2
unnamed: J3.1, U1.4
unnamed: J3.3, U1.5
unnamed: J3.5, U1.6
unnamed: J3.7, U1.7
unnamed: J4.1, U1.9
unnamed: J4.3, U1.10
unnamed: J4.5, U1.11
unnamed: J4.7, U1.12

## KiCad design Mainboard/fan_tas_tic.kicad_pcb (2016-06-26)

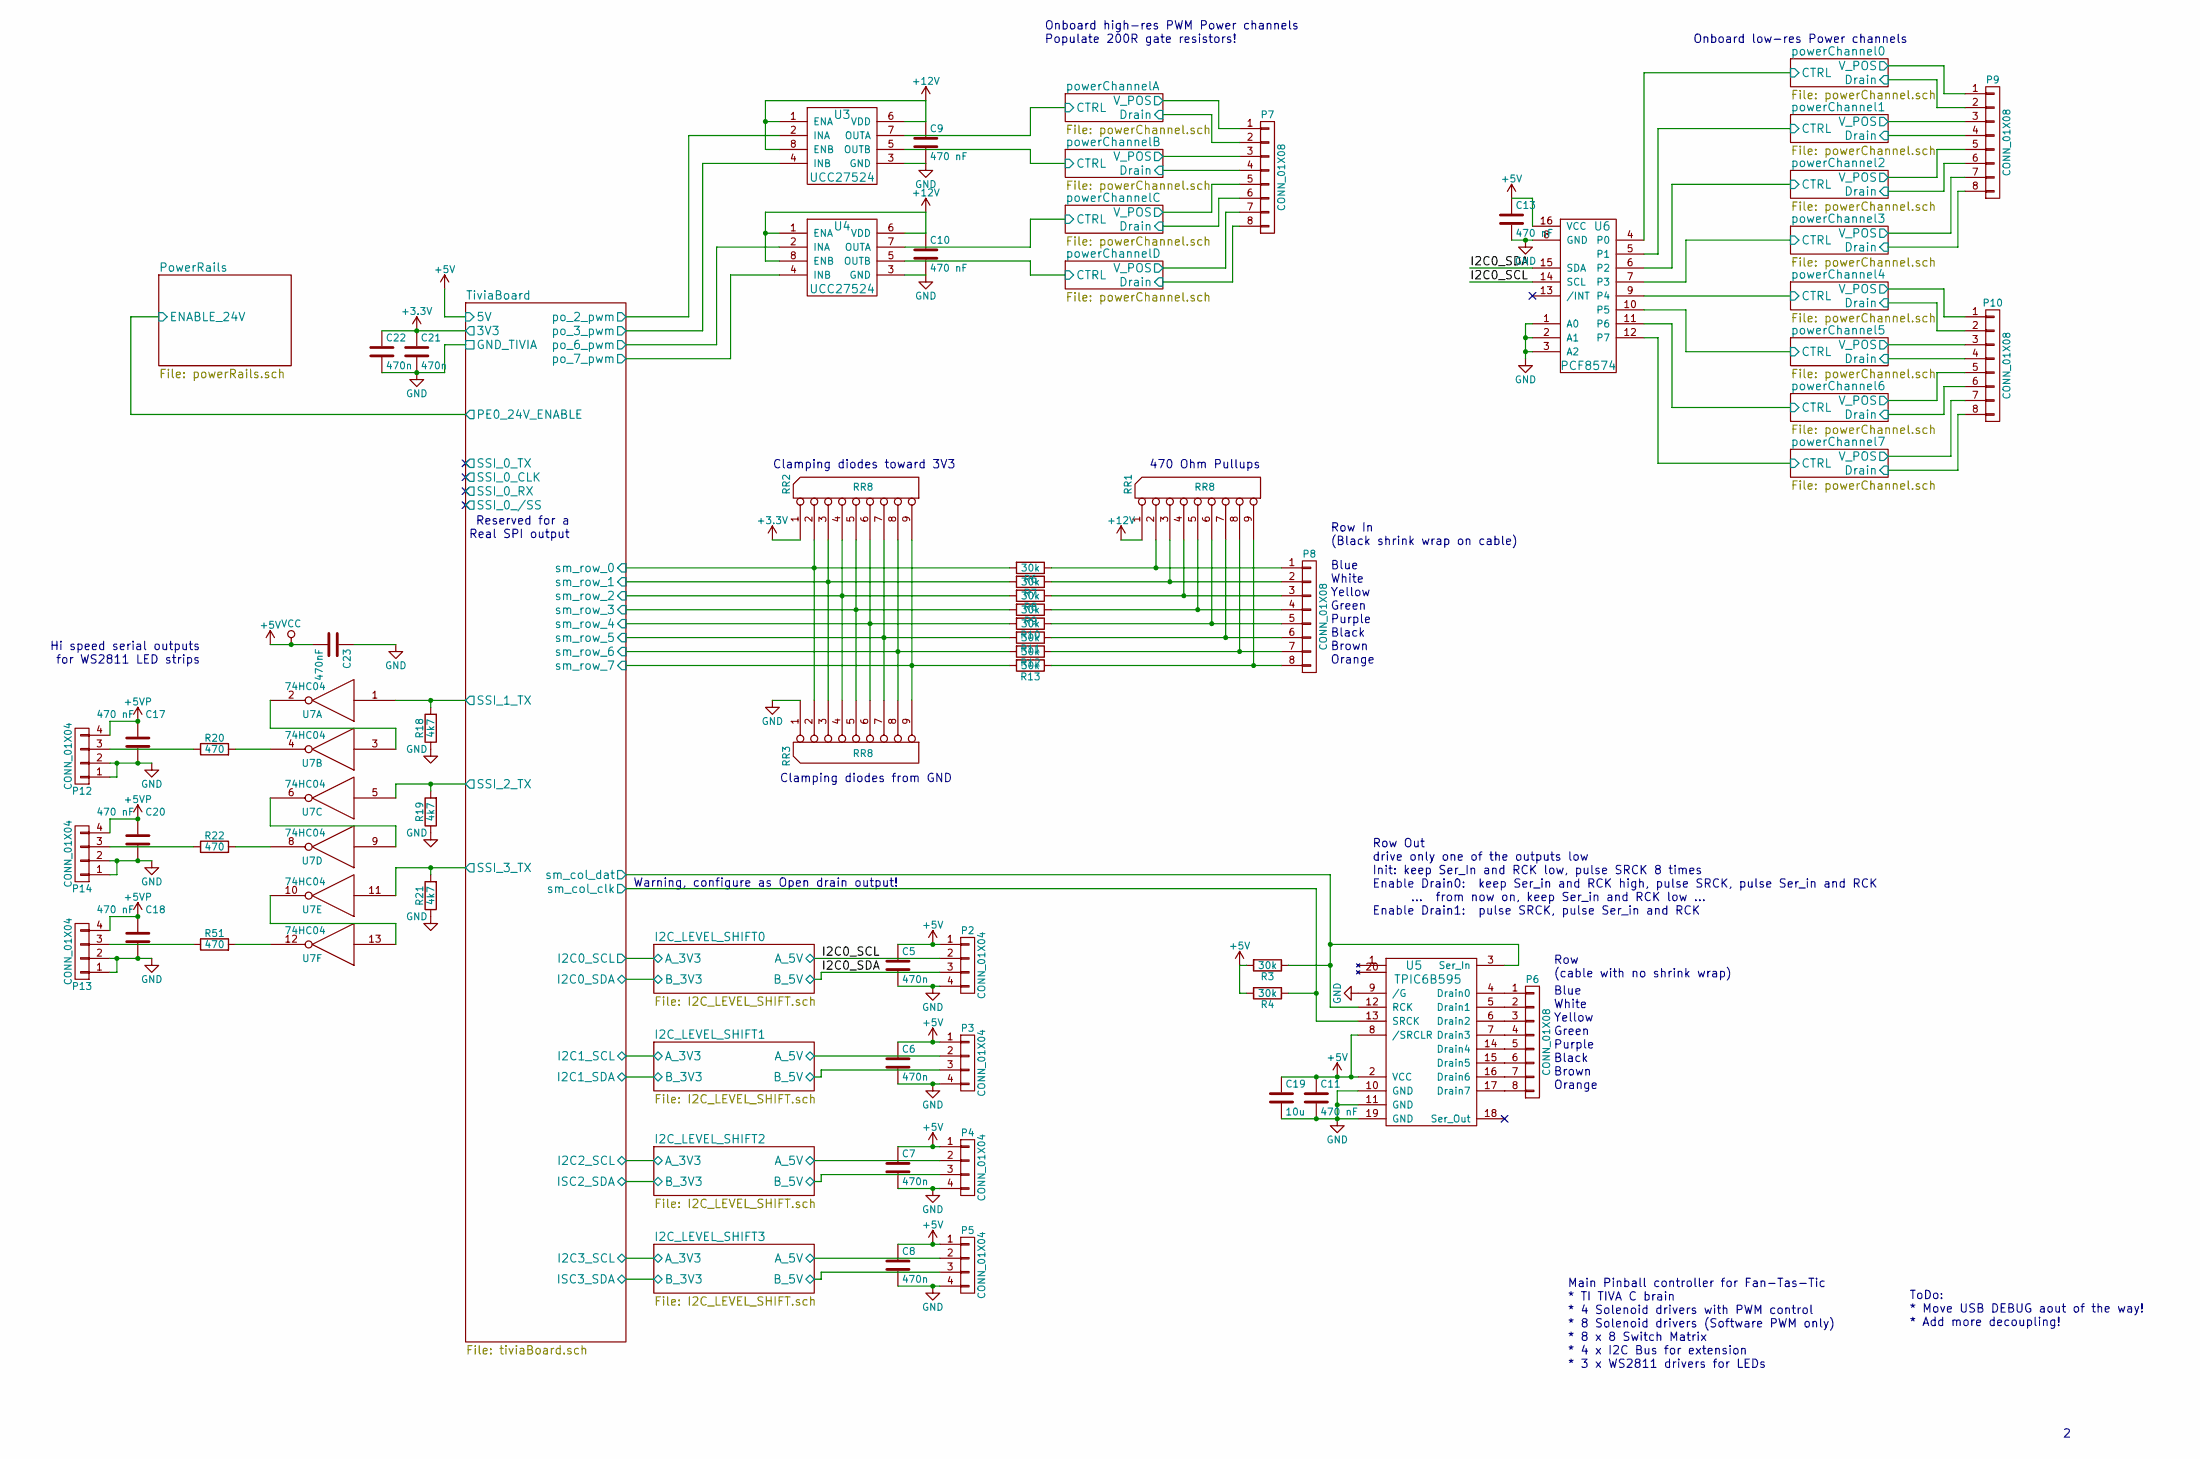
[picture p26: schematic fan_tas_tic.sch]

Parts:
C5, C6, C7, C8, C21, C22: 470n; C_0805_HandSoldering
C9, C10, C11, C13, C17, C18, C20: 470 nF; C_0805_HandSoldering
C19: 10u; C_1210_HandSoldering
C23: 470nF; C_0805_HandSoldering
P2, P3, P4, P5: CONN_01X04; Pin_Header_Straight_1x04
P6, P8: CONN_01X08; Pin_Header_Straight_1x08
P7, P9, P10: CONN_01X08; HT396_8
P12, P13, P14: CONN_01X04; HT396_4
R3, R4, R6, R7, R8, R9, R10, R11, R12, R13: 30k; R_0805_HandSoldering
R18, R19, R21: 4k7; R_0805_HandSoldering
R20, R22: 470; R_0805_HandSoldering
R51: 470; Resistor_Vertical_RM5mm
RR1, RR2, RR3: RR8; Resistor_Array_SIP8
U3, U4: UCC27524; DIP-8_W7.62mm_LongPads
U5: TPIC6B595; DIP-20_W7.62mm_LongPads
U6: PCF8574; SOIC-16_7.5x10.3mm_Pitch1.27mm
U7: 74HC04; DIP-14_W7.62mm_LongPads

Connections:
+3V3: C21.1, C22.1, RR2.1 (COM); also elsewhere on the board
+5V: C5.1, C6.1, C7.1, C8.1, C11.1, C13.1, C19.1, C23.2, P2.1, P3.1, P4.1, P5.1, R3.2, R4.2, U5.2 (VCC), U5.8 (/SRCLR), U6.16 (VCC), U7.14 (VCC); also elsewhere on the board
+5VP: C17.1, C18.1, C20.1, P12.4, P13.4, P14.4; also elsewhere on the board
+12V: C9.1, C10.1, RR1.1 (COM), U3.1 (ENA), U3.6 (VDD), U3.8 (ENB), U4.1 (ENA), U4.6 (VDD), U4.8 (ENB); also elsewhere on the board
+24V: P7.1, P7.3, P7.5, P7.7, P9.1, P9.3, P9.5, P9.7, P10.1, P10.3, P10.5, P10.7; also elsewhere on the board
/I2C_LEVEL_SHIFT0/A_5V: P2.2, U6.14 (SCL); also elsewhere on the board
/I2C_LEVEL_SHIFT0/B_5V: P2.3, U6.15 (SDA); also elsewhere on the board
/I2C_LEVEL_SHIFT1/A_5V: P3.2; also elsewhere on the board
/I2C_LEVEL_SHIFT1/B_5V: P3.3; also elsewhere on the board
/I2C_LEVEL_SHIFT2/A_5V: P4.2; also elsewhere on the board
/I2C_LEVEL_SHIFT2/B_5V: P4.3; also elsewhere on the board
/I2C_LEVEL_SHIFT3/A_5V: P5.2; also elsewhere on the board
/I2C_LEVEL_SHIFT3/B_5V: P5.3; also elsewhere on the board
/TiviaBoard/SSI_1_TX: R18.2, U7.1; also elsewhere on the board
/TiviaBoard/SSI_2_TX: R19.2, U7.5; also elsewhere on the board
/TiviaBoard/SSI_3_TX: R21.2, U7.11; also elsewhere on the board
/TiviaBoard/po_2_pwm: U3.2 (INA); also elsewhere on the board
/TiviaBoard/po_3_pwm: U3.4 (INB); also elsewhere on the board
/TiviaBoard/po_6_pwm: U4.2 (INA); also elsewhere on the board
/TiviaBoard/po_7_pwm: U4.4 (INB); also elsewhere on the board
/TiviaBoard/sm_col_clk: R4.1, U5.13 (SRCK); also elsewhere on the board
/TiviaBoard/sm_col_dat: R3.1, U5.3 (Ser_In), U5.12 (RCK); also elsewhere on the board
/TiviaBoard/sm_row_0: R6.2, RR2.2, RR3.2; also elsewhere on the board
/TiviaBoard/sm_row_1: R7.2, RR2.3, RR3.3; also elsewhere on the board
/TiviaBoard/sm_row_2: R8.2, RR2.4, RR3.4; also elsewhere on the board
/TiviaBoard/sm_row_3: R9.2, RR2.5, RR3.5; also elsewhere on the board
/TiviaBoard/sm_row_4: R10.2, RR2.6, RR3.6; also elsewhere on the board
/TiviaBoard/sm_row_5: R11.2, RR2.7, RR3.7; also elsewhere on the board
/TiviaBoard/sm_row_6: R12.2, RR2.8, RR3.8; also elsewhere on the board
/TiviaBoard/sm_row_7: R13.2, RR2.9, RR3.9; also elsewhere on the board
/powerChannel0/CTRL: U6.4 (P0); also elsewhere on the board
/powerChannel0/DRAIN: P9.2; also elsewhere on the board
/powerChannel1/CTRL: U6.5 (P1); also elsewhere on the board
/powerChannel1/DRAIN: P9.4; also elsewhere on the board
/powerChannel2/CTRL: U6.6 (P2); also elsewhere on the board
/powerChannel2/DRAIN: P9.6; also elsewhere on the board
/powerChannel3/CTRL: U6.7 (P3); also elsewhere on the board
/powerChannel3/DRAIN: P9.8; also elsewhere on the board
/powerChannel4/CTRL: U6.9 (P4); also elsewhere on the board
/powerChannel4/DRAIN: P10.2; also elsewhere on the board
/powerChannel5/CTRL: U6.10 (P5); also elsewhere on the board
/powerChannel5/DRAIN: P10.4; also elsewhere on the board
/powerChannel6/CTRL: U6.11 (P6); also elsewhere on the board
/powerChannel6/DRAIN: P10.6; also elsewhere on the board
/powerChannel7/CTRL: U6.12 (P7); also elsewhere on the board
/powerChannel7/DRAIN: P10.8; also elsewhere on the board
/powerChannelA/CTRL: U3.7 (OUTA); also elsewhere on the board
/powerChannelA/DRAIN: P7.2; also elsewhere on the board
/powerChannelB/CTRL: U3.5 (OUTB); also elsewhere on the board
/powerChannelB/DRAIN: P7.4; also elsewhere on the board
/powerChannelC/CTRL: U4.7 (OUTA); also elsewhere on the board
/powerChannelC/DRAIN: P7.6; also elsewhere on the board
/powerChannelD/CTRL: U4.5 (OUTB); also elsewhere on the board
/powerChannelD/DRAIN: P7.8; also elsewhere on the board
GND: C5.2, C6.2, C7.2, C8.2, C9.2, C10.2, C11.2, C13.2, C17.2, C18.2, C19.2, C20.2, C21.2, C22.2, C23.1, P2.4, P3.4, P4.4, P5.4, P12.1, P12.2, P13.1, P13.2, P14.1, P14.2, R18.1, R19.1, R21.1, RR3.1 (COM), U3.3 (GND), U4.3 (GND), U5.9 (/G), U5.10 (GND), U5.11 (GND), U5.19 (GND), U6.1 (A0), U6.2 (A1), U6.3 (A2), U6.8 (GND), U7.7 (GND); also elsewhere on the board
unnamed: P6.1, U5.4 (Drain0)
unnamed: P6.2, U5.5 (Drain1)
unnamed: P6.3, U5.6 (Drain2)
unnamed: P6.4, U5.7 (Drain3)
unnamed: P6.5, U5.14 (Drain4)
unnamed: P6.6, U5.15 (Drain5)
unnamed: P6.7, U5.16 (Drain6)
unnamed: P6.8, U5.17 (Drain7)
unnamed: P8.1, R6.1, RR1.2
unnamed: P8.2, R7.1, RR1.3
unnamed: P8.3, R8.1, RR1.4
unnamed: P8.4, R9.1, RR1.5
unnamed: P8.5, R10.1, RR1.6
unnamed: P8.6, R11.1, RR1.7
unnamed: P8.7, R12.1, RR1.8
unnamed: P8.8, R13.1, RR1.9
unnamed: P12.3, R20.1
unnamed: P13.3, R51.1
unnamed: P14.3, R22.1
unnamed: R20.2, U7.4
unnamed: R22.2, U7.8
unnamed: R51.2, U7.12
unnamed: U7.2, U7.3
unnamed: U7.6, U7.9
unnamed: U7.10, U7.13

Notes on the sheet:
Row Out drive only one of the outputs low Init: keep Ser_In and RCK low, pulse SRCK 8 times Enable Drain0: keep Ser_in and RCK high, pulse SRCK, pulse Ser_in and RCK ... from now on, keep Ser_in and RCK low ... Enable Drain1: pulse SRCK, pulse Ser_in and RCK
Row In (Black shrink wrap on cable)
Onboard high-res PWM Power channels Populate 200R gate resistors!
Onboard low-res Power channels
Warning, configure as Open drain output!
Main Pinball controller for Fan-Tas-Tic * TI TIVA C brain * 4 Solenoid drivers with PWM control * 8 Solenoid drivers (Software PWM only) * 8 x 8 Switch Matrix * 4 x I2C Bus for extension * 3 x WS2811 drivers for LEDs
Hi speed serial outputs for WS2811 LED strips
470 Ohm Pullups
Clamping diodes toward 3V3
Clamping diodes from GND
Reserved for a Real SPI output
ToDo: * Move USB DEBUG aout of the way! * Add more decoupling!
Blue White Yellow Green Purple Black Brown Orange
Row (cable with no shrink wrap)

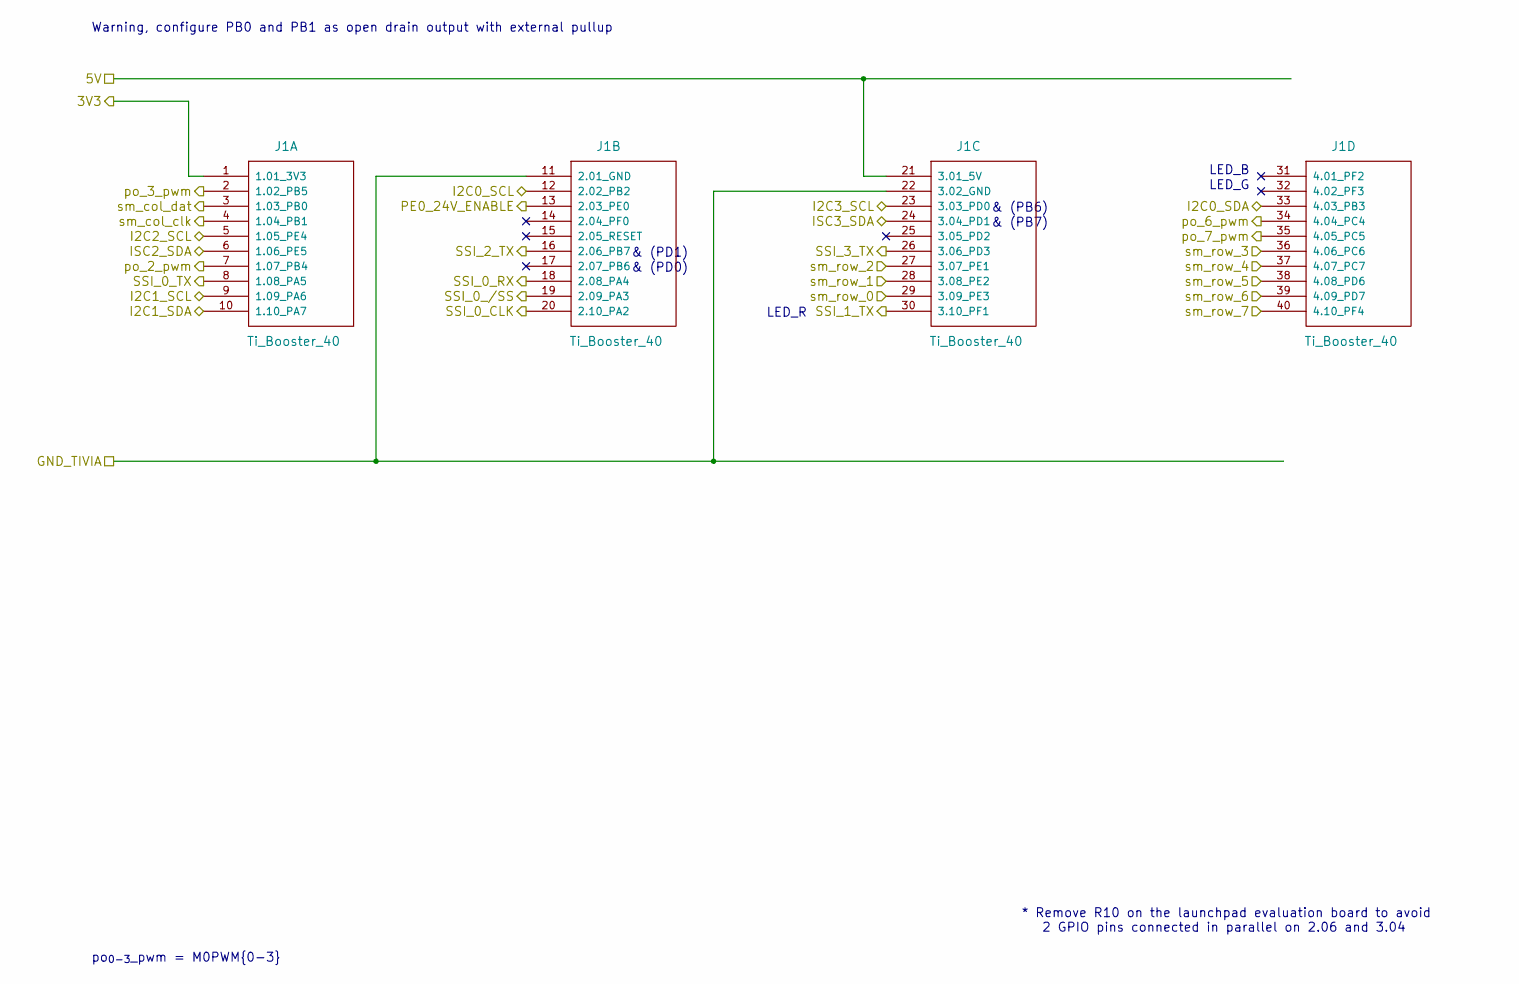
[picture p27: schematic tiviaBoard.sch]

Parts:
J1: Ti_Booster_40; Tivia_Launch_Pad

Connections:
+3V3: J1.1 (1.01_3V3); also elsewhere on the board
+5V: J1.21 (3.01_5V); also elsewhere on the board
/I2C_LEVEL_SHIFT0/A_3V3: J1.12 (2.02_PB2); also elsewhere on the board
/I2C_LEVEL_SHIFT0/B_3V3: J1.33 (4.03_PB3); also elsewhere on the board
/I2C_LEVEL_SHIFT1/A_3V3: J1.9 (1.09_PA6); also elsewhere on the board
/I2C_LEVEL_SHIFT1/B_3V3: J1.10 (1.10_PA7); also elsewhere on the board
/I2C_LEVEL_SHIFT2/A_3V3: J1.5 (1.05_PE4); also elsewhere on the board
/I2C_LEVEL_SHIFT2/B_3V3: J1.6 (1.06_PE5); also elsewhere on the board
/I2C_LEVEL_SHIFT3/A_3V3: J1.23 (3.03_PD0); also elsewhere on the board
/I2C_LEVEL_SHIFT3/B_3V3: J1.24 (3.04_PD1); also elsewhere on the board
/PowerRails/ENABLE_24V: J1.13 (2.03_PE0); also elsewhere on the board
/TiviaBoard/SSI_1_TX: J1.30 (3.10_PF1); also elsewhere on the board
/TiviaBoard/SSI_2_TX: J1.16 (2.06_PB7); also elsewhere on the board
/TiviaBoard/SSI_3_TX: J1.26 (3.06_PD3); also elsewhere on the board
/TiviaBoard/po_2_pwm: J1.7 (1.07_PB4); also elsewhere on the board
/TiviaBoard/po_3_pwm: J1.2 (1.02_PB5); also elsewhere on the board
/TiviaBoard/po_6_pwm: J1.34 (4.04_PC4); also elsewhere on the board
/TiviaBoard/po_7_pwm: J1.35 (4.05_PC5); also elsewhere on the board
/TiviaBoard/sm_col_clk: J1.4 (1.04_PB1); also elsewhere on the board
/TiviaBoard/sm_col_dat: J1.3 (1.03_PB0); also elsewhere on the board
/TiviaBoard/sm_row_0: J1.29 (3.09_PE3); also elsewhere on the board
/TiviaBoard/sm_row_1: J1.28 (3.08_PE2); also elsewhere on the board
/TiviaBoard/sm_row_2: J1.27 (3.07_PE1); also elsewhere on the board
/TiviaBoard/sm_row_3: J1.36 (4.06_PC6); also elsewhere on the board
/TiviaBoard/sm_row_4: J1.37 (4.07_PC7); also elsewhere on the board
/TiviaBoard/sm_row_5: J1.38 (4.08_PD6); also elsewhere on the board
/TiviaBoard/sm_row_6: J1.39 (4.09_PD7); also elsewhere on the board
/TiviaBoard/sm_row_7: J1.40 (4.10_PF4); also elsewhere on the board
GND: J1.11 (2.01_GND), J1.22 (3.02_GND); also elsewhere on the board

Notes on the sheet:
po_{0-3}_pwm = M0PWM{0-3}
Warning, configure PB0 and PB1 as open drain output with external pullup
LED_R
LED_B
LED_G
& (PD1)
& (PD0)
& (PB6)
& (PB7)
* Remove R10 on the launchpad evaluation board to avoid 2 GPIO pins connected in parallel on 2.06 and 3.04

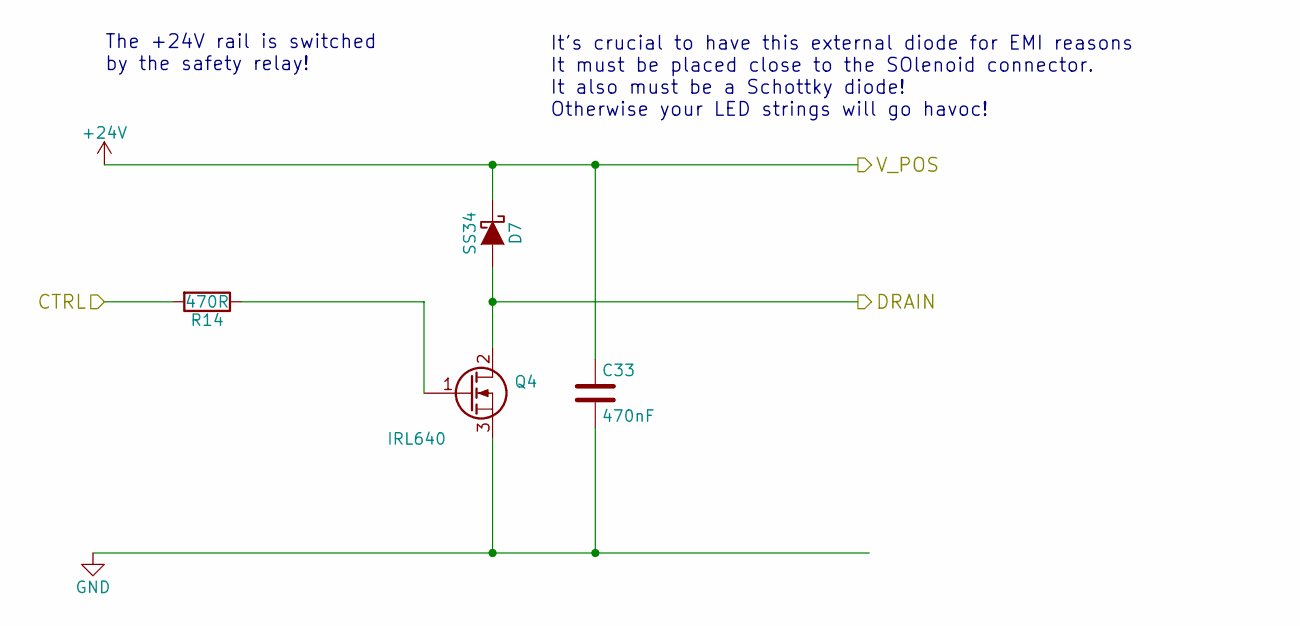
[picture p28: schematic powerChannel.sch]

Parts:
C25: 470nF; C_0805_HandSoldering
D8: SS34; SMC-RM10_Universal_Handsoldering
Q5: IRL640; TO-220_Neutral123_Vertical_LargePads
R23: 470R; R_0805_HandSoldering

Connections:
+24V: C25.1, D8.1 (K); also elsewhere on the board
/powerChannel0/CTRL: R23.2; also elsewhere on the board
/powerChannel0/DRAIN: D8.2 (A), Q5.2 (D); also elsewhere on the board
GND: C25.2, Q5.3 (S); also elsewhere on the board
unnamed: Q5.1 (G), R23.1

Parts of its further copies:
C12, C14, C15, C26, C27, C28, C29, C30, C31, C32, C33: 470nF; C_0805_HandSoldering
D4, D5, D6, D7, D9, D10, D11, D13, D14, D15, D16: SS34; SMC-RM10_Universal_Handsoldering
Q1, Q2, Q3, Q4, Q6, Q7, Q8, Q9, Q10, Q11, Q12: IRL640; TO-220_Neutral123_Vertical_LargePads
R1, R2, R5, R14, R24, R25, R26, R27, R28, R29, R30: 470R; R_0805_HandSoldering

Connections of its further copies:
+24V: C12.1, C14.1, C15.1, C26.1, C27.1, C28.1, C29.1, C30.1, C31.1, C32.1, C33.1, D4.1 (K), D5.1 (K), D6.1 (K), D7.1 (K), D9.1 (K), D10.1 (K), D11.1 (K), D13.1 (K), D14.1 (K), D15.1 (K), D16.1 (K); also elsewhere on the board
/powerChannel1/CTRL: R24.2; also elsewhere on the board
/powerChannel1/DRAIN: D9.2 (A), Q6.2 (D); also elsewhere on the board
/powerChannel2/CTRL: R25.2; also elsewhere on the board
/powerChannel2/DRAIN: D10.2 (A), Q7.2 (D); also elsewhere on the board
/powerChannel3/CTRL: R26.2; also elsewhere on the board
/powerChannel3/DRAIN: D11.2 (A), Q8.2 (D); also elsewhere on the board
/powerChannel4/CTRL: R27.2; also elsewhere on the board
/powerChannel4/DRAIN: D13.2 (A), Q9.2 (D); also elsewhere on the board
/powerChannel5/CTRL: R28.2; also elsewhere on the board
/powerChannel5/DRAIN: D14.2 (A), Q10.2 (D); also elsewhere on the board
/powerChannel6/CTRL: R29.2; also elsewhere on the board
/powerChannel6/DRAIN: D15.2 (A), Q11.2 (D); also elsewhere on the board
/powerChannel7/CTRL: R30.2; also elsewhere on the board
/powerChannel7/DRAIN: D16.2 (A), Q12.2 (D); also elsewhere on the board
/powerChannelA/CTRL: R1.2; also elsewhere on the board
/powerChannelA/DRAIN: D4.2 (A), Q1.2 (D); also elsewhere on the board
/powerChannelB/CTRL: R2.2; also elsewhere on the board
/powerChannelB/DRAIN: D5.2 (A), Q2.2 (D); also elsewhere on the board
/powerChannelC/CTRL: R5.2; also elsewhere on the board
/powerChannelC/DRAIN: D6.2 (A), Q3.2 (D); also elsewhere on the board
/powerChannelD/CTRL: R14.2; also elsewhere on the board
/powerChannelD/DRAIN: D7.2 (A), Q4.2 (D); also elsewhere on the board
GND: C12.2, C14.2, C15.2, C26.2, C27.2, C28.2, C29.2, C30.2, C31.2, C32.2, C33.2, Q1.3 (S), Q2.3 (S), Q3.3 (S), Q4.3 (S), Q6.3 (S), Q7.3 (S), Q8.3 (S), Q9.3 (S), Q10.3 (S), Q11.3 (S), Q12.3 (S); also elsewhere on the board
unnamed: Q1.1 (G), R1.1
unnamed: Q2.1 (G), R2.1
unnamed: Q3.1 (G), R5.1
unnamed: Q4.1 (G), R14.1
unnamed: Q6.1 (G), R24.1
unnamed: Q7.1 (G), R25.1
unnamed: Q8.1 (G), R26.1
unnamed: Q9.1 (G), R27.1
unnamed: Q10.1 (G), R28.1
unnamed: Q11.1 (G), R29.1
unnamed: Q12.1 (G), R30.1

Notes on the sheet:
It's crucial to have this external diode for EMI reasons It must be placed close to the SOlenoid connector. It also must be a Schottky diode! Otherwise your LED strings will go havoc!
The +24V rail is switched by the safety relay!

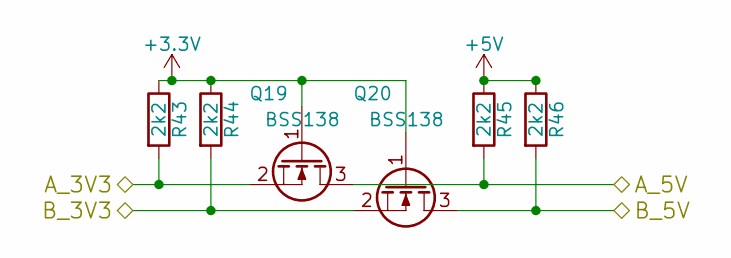
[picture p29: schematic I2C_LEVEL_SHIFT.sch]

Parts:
Q13, Q14: BSS138; SOT-23_Handsoldering
R31, R32, R33, R34: 2k2; R_0805_HandSoldering

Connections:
+3V3: Q13.1 (G), Q14.1 (G), R31.1, R32.1; also elsewhere on the board
+5V: R33.1, R34.1; also elsewhere on the board
/I2C_LEVEL_SHIFT0/A_3V3: Q13.2 (S), R31.2; also elsewhere on the board
/I2C_LEVEL_SHIFT0/A_5V: Q13.3 (D), R33.2; also elsewhere on the board
/I2C_LEVEL_SHIFT0/B_3V3: Q14.2 (S), R32.2; also elsewhere on the board
/I2C_LEVEL_SHIFT0/B_5V: Q14.3 (D), R34.2; also elsewhere on the board

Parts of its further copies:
Q15, Q16, Q17, Q18, Q19, Q20: BSS138; SOT-23_Handsoldering
R35, R36, R37, R38, R39, R40, R41, R42, R43, R44, R45, R46: 2k2; R_0805_HandSoldering

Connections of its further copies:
+3V3: Q15.1 (G), Q16.1 (G), Q17.1 (G), Q18.1 (G), Q19.1 (G), Q20.1 (G), R35.1, R36.1, R39.1, R40.1, R43.1, R44.1; also elsewhere on the board
+5V: R37.1, R38.1, R41.1, R42.1, R45.1, R46.1; also elsewhere on the board
/I2C_LEVEL_SHIFT1/A_3V3: Q15.2 (S), R35.2; also elsewhere on the board
/I2C_LEVEL_SHIFT1/A_5V: Q15.3 (D), R37.2; also elsewhere on the board
/I2C_LEVEL_SHIFT1/B_3V3: Q16.2 (S), R36.2; also elsewhere on the board
/I2C_LEVEL_SHIFT1/B_5V: Q16.3 (D), R38.2; also elsewhere on the board
/I2C_LEVEL_SHIFT2/A_3V3: Q17.2 (S), R39.2; also elsewhere on the board
/I2C_LEVEL_SHIFT2/A_5V: Q17.3 (D), R41.2; also elsewhere on the board
/I2C_LEVEL_SHIFT2/B_3V3: Q18.2 (S), R40.2; also elsewhere on the board
/I2C_LEVEL_SHIFT2/B_5V: Q18.3 (D), R42.2; also elsewhere on the board
/I2C_LEVEL_SHIFT3/A_3V3: Q19.2 (S), R43.2; also elsewhere on the board
/I2C_LEVEL_SHIFT3/A_5V: Q19.3 (D), R45.2; also elsewhere on the board
/I2C_LEVEL_SHIFT3/B_3V3: Q20.2 (S), R44.2; also elsewhere on the board
/I2C_LEVEL_SHIFT3/B_5V: Q20.3 (D), R46.2; also elsewhere on the board

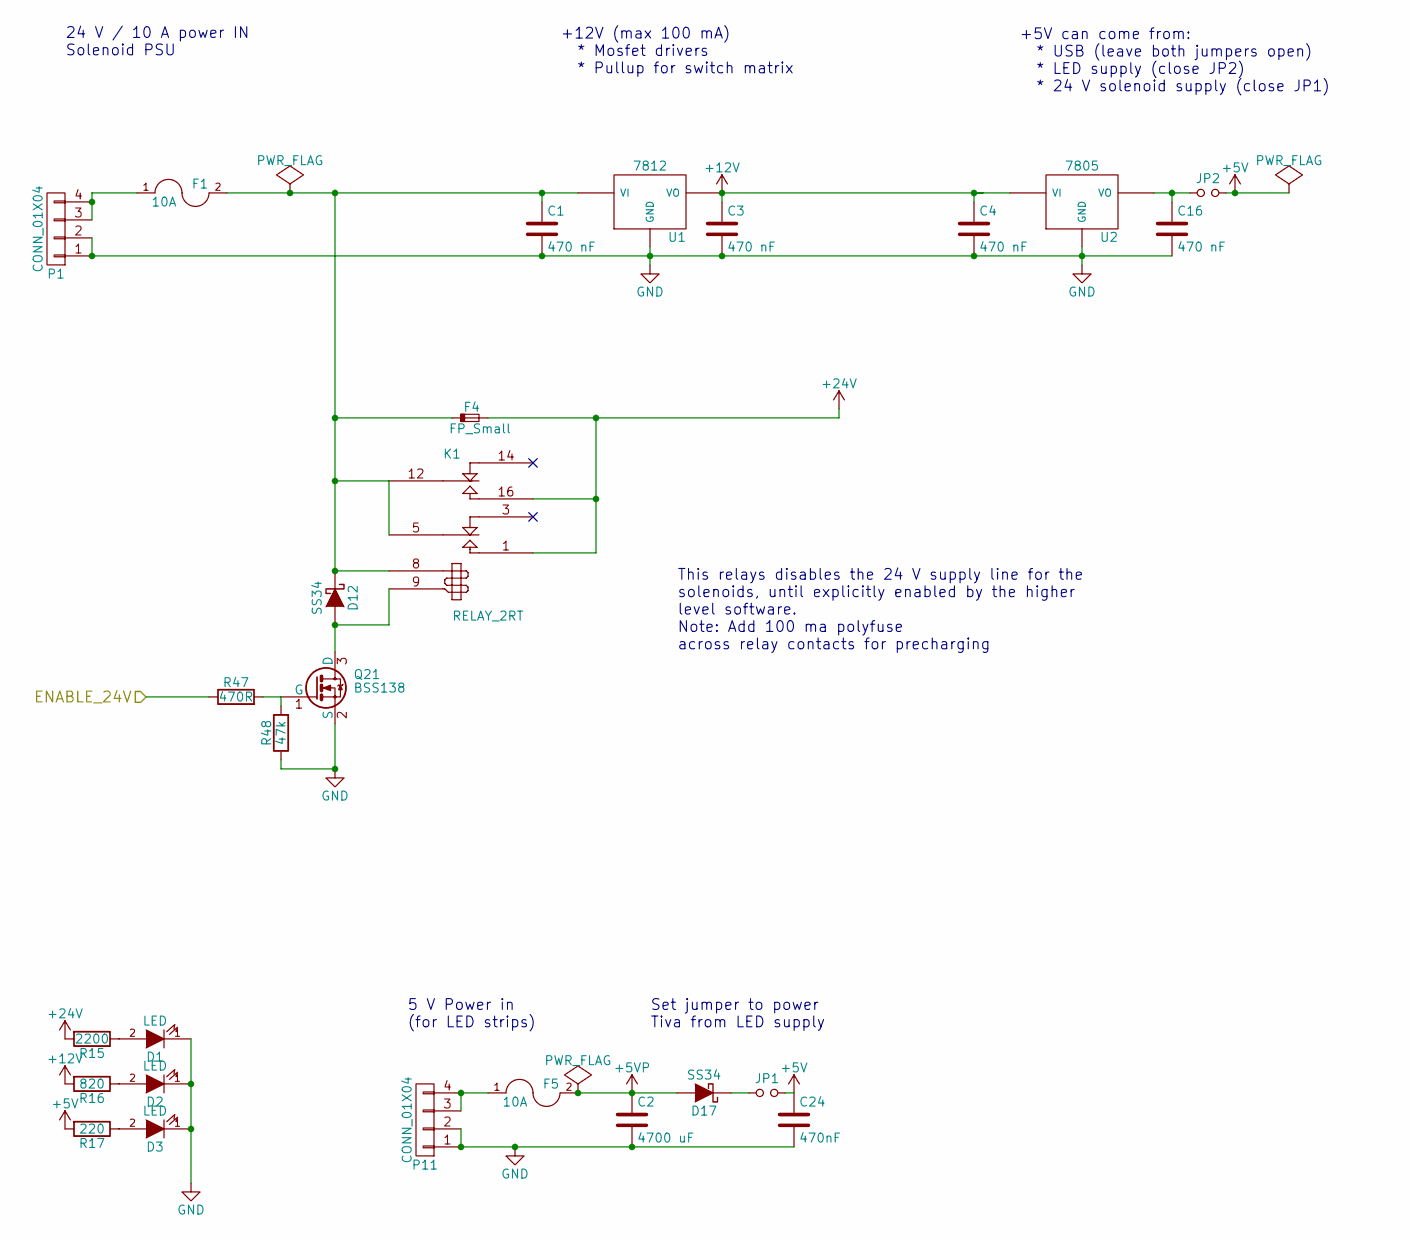
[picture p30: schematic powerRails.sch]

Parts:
C1, C3, C4, C16: 470 nF; C_0805_HandSoldering
C2: 4700 uF; C_Radial_D10_L16_P5
C24: 470nF; C_0805_HandSoldering
D1, D2, D3: LED; LED-0805
D12, D17: SS34; SMC-RM10_Universal_Handsoldering
F1, F5: 10A; Fuseholder5x20_horiz_open_universal_Type-III
F4: FP_Small; Fuse_SMD1206_HandSoldering
JP1, JP2: Jumper_NO_Small; Pin_Header_Straight_1x02
K1: RELAY_2RT; Relay_SPDT_RM5mm
P1, P11: CONN_01X04; HT396_4
Q21: BSS138; SOT-23
R15: 2200; R_0805_HandSoldering
R16: 820; R_0805_HandSoldering
R17: 220; R_0805_HandSoldering
R47: 470R; R_0805_HandSoldering
R48: 47k; R_0805_HandSoldering
U1: 7812; TO-220_Neutral123_Vertical_LargePads
U2: 7805; TO-220_Neutral123_Vertical_LargePads

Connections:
+5V: C24.1, JP1.2, JP2.2, R17.2; also elsewhere on the board
+5VP: C2.1, D17.2 (A), F5.2; also elsewhere on the board
+12V: C3.1, C4.1, R16.2, U1.VO, U2.VI; also elsewhere on the board
+24V: F4.2, K1.1 (T1), K1.16 (T2), R15.2; also elsewhere on the board
/PowerRails/ENABLE_24V: R47.1; also elsewhere on the board
GND: C1.2, C2.2, C3.2, C4.2, C16.2, C24.2, D1.1 (K), D2.1 (K), D3.1 (K), P1.1, P1.2, P11.1, P11.2, Q21.2 (S), R48.1, U1.GND, U2.GND; also elsewhere on the board
unnamed: C1.1, D12.1 (K), F1.2, F4.1, K1.5 (C1), K1.8, K1.12 (C2), U1.VI
unnamed: C16.1, JP2.1, U2.VO
unnamed: D1.2 (A), R15.1
unnamed: D2.2 (A), R16.1
unnamed: D3.2 (A), R17.1
unnamed: D12.2 (A), K1.9, Q21.3 (D)
unnamed: D17.1 (K), JP1.1
unnamed: F1.1, P1.3, P1.4
unnamed: F5.1, P11.3, P11.4
unnamed: Q21.1 (G), R47.2, R48.2

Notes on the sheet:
24 V / 10 A power IN Solenoid PSU
+5V can come from: * USB (leave both jumpers open) * LED supply (close JP2) * 24 V solenoid supply (close JP1)
5 V Power in (for LED strips)
Set jumper to power Tiva from LED supply
This relays disables the 24 V supply line for the solenoids, until explicitly enabled by the higher level software. Note: Add 100 ma polyfuse across relay contacts for precharging
+12V (max 100 mA) * Mosfet drivers * Pullup for switch matrix

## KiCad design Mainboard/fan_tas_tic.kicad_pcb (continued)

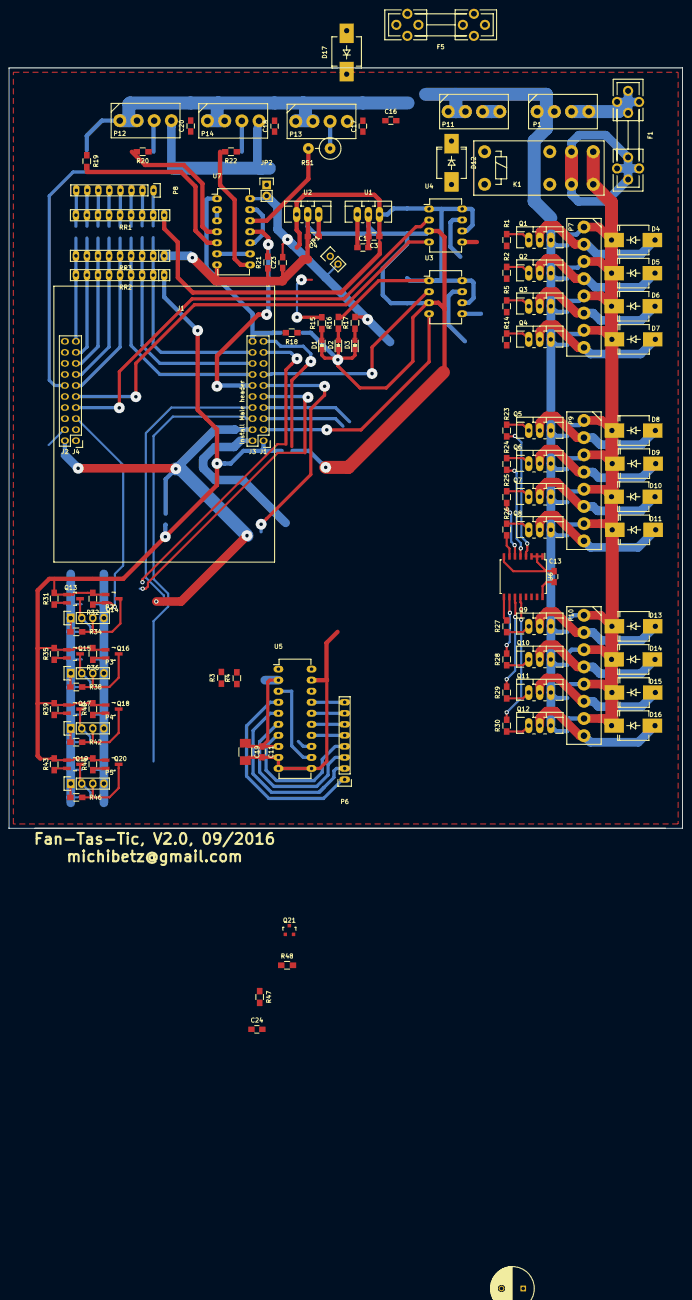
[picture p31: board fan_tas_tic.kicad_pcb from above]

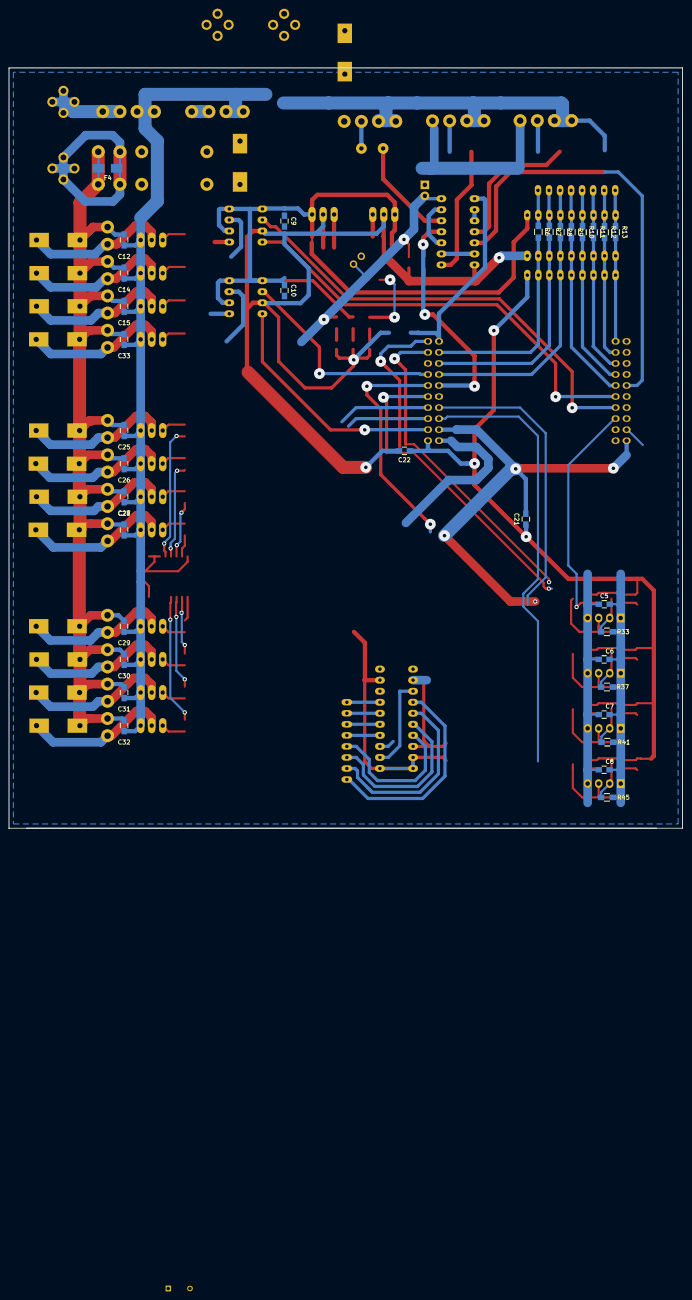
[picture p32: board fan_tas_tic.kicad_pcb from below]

Board: 2 copper layers, 155.0 x 175.0 mm, 151 parts (33 on the bottom side), 111 nets.

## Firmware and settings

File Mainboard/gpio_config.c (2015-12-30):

//*****************************************************************************
// Copyright (c) 2014 Texas Instruments Incorporated.  All rights reserved.
// Software License Agreement
// 
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
//   Redistributions of source code must retain the above copyright
//   notice, this list of conditions and the following disclaimer.
// 
//   Redistributions in binary form must reproduce the above copyright
//   notice, this list of conditions and the following disclaimer in the
//   documentation and/or other materials provided with the  
//   distribution.
// 
//   Neither the name of Texas Instruments Incorporated nor the names of
//   its contributors may be used to endorse or promote products derived
//   from this software without specific prior written permission.
// 
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
// This file was automatically generated by the Tiva C Series PinMux Utility
// Version: 1.0.4
//
//*****************************************************************************

#include <stdint.h>
#include <stdbool.h>
#include "gpio_config.h"
#include "inc/hw_types.h"
#include "inc/hw_memmap.h"
#include "inc/hw_gpio.h"
#include "driverlib/sysctl.h"
#include "driverlib/pin_map.h"
#include "driverlib/rom_map.h"
#include "driverlib/gpio.h"

//*****************************************************************************
void
PortFunctionInit(void)
{
    //
    // Enable Peripheral Clocks 
    //
    MAP_SysCtlPeripheralEnable(SYSCTL_PERIPH_I2C0);
    MAP_SysCtlPeripheralEnable(SYSCTL_PERIPH_I2C1);
    MAP_SysCtlPeripheralEnable(SYSCTL_PERIPH_I2C2);
    MAP_SysCtlPeripheralEnable(SYSCTL_PERIPH_I2C3);
    MAP_SysCtlPeripheralEnable(SYSCTL_PERIPH_PWM0);
    MAP_SysCtlPeripheralEnable(SYSCTL_PERIPH_USB0);
    MAP_SysCtlPeripheralEnable(SYSCTL_PERIPH_GPIOA);
    MAP_SysCtlPeripheralEnable(SYSCTL_PERIPH_GPIOB);
    MAP_SysCtlPeripheralEnable(SYSCTL_PERIPH_GPIOC);
    MAP_SysCtlPeripheralEnable(SYSCTL_PERIPH_GPIOD);
    MAP_SysCtlPeripheralEnable(SYSCTL_PERIPH_GPIOE);

    //
    // Enable pin PB3 for I2C0 I2C0SDA
    //
    MAP_GPIOPinConfigure(GPIO_PB3_I2C0SDA);
    MAP_GPIOPinTypeI2C(GPIO_PORTB_BASE, GPIO_PIN_3);

    //
    // Enable pin PB2 for I2C0 I2C0SCL
    //
    MAP_GPIOPinConfigure(GPIO_PB2_I2C0SCL);
    MAP_GPIOPinTypeI2CSCL(GPIO_PORTB_BASE, GPIO_PIN_2);

    //
    // Enable pin PA6 for I2C1 I2C1SCL
    //
    MAP_GPIOPinConfigure(GPIO_PA6_I2C1SCL);
    MAP_GPIOPinTypeI2CSCL(GPIO_PORTA_BASE, GPIO_PIN_6);

    //
    // Enable pin PA7 for I2C1 I2C1SDA
    //
    MAP_GPIOPinConfigure(GPIO_PA7_I2C1SDA);
    MAP_GPIOPinTypeI2C(GPIO_PORTA_BASE, GPIO_PIN_7);

    //
    // Enable pin PE5 for I2C2 I2C2SDA
    //
    MAP_GPIOPinConfigure(GPIO_PE5_I2C2SDA);
    MAP_GPIOPinTypeI2C(GPIO_PORTE_BASE, GPIO_PIN_5);

    //
    // Enable pin PE4 for I2C2 I2C2SCL
    //
    MAP_GPIOPinConfigure(GPIO_PE4_I2C2SCL);
    MAP_GPIOPinTypeI2CSCL(GPIO_PORTE_BASE, GPIO_PIN_4);

    //
    // Enable pin PD1 for I2C3 I2C3SDA
    //
    MAP_GPIOPinConfigure(GPIO_PD1_I2C3SDA);
    MAP_GPIOPinTypeI2C(GPIO_PORTD_BASE, GPIO_PIN_1);

    //
    // Enable pin PD0 for I2C3 I2C3SCL
    //
    MAP_GPIOPinConfigure(GPIO_PD0_I2C3SCL);
    MAP_GPIOPinTypeI2CSCL(GPIO_PORTD_BASE, GPIO_PIN_0);

    //
    // Enable pin PB6 for PWM0 M0PWM0
    //
    MAP_GPIOPinConfigure(GPIO_PB6_M0PWM0);
    MAP_GPIOPinTypePWM(GPIO_PORTB_BASE, GPIO_PIN_6);

    //
    // Enable pin PB5 for PWM0 M0PWM3
    //
    MAP_GPIOPinConfigure(GPIO_PB5_M0PWM3);
    MAP_GPIOPinTypePWM(GPIO_PORTB_BASE, GPIO_PIN_5);

    //
    // Enable pin PB7 for PWM0 M0PWM1
    //
    MAP_GPIOPinConfigure(GPIO_PB7_M0PWM1);
    MAP_GPIOPinTypePWM(GPIO_PORTB_BASE, GPIO_PIN_7);

    //
    // Enable pin PC4 for PWM0 M0PWM6
    //
    MAP_GPIOPinConfigure(GPIO_PC4_M0PWM6);
    MAP_GPIOPinTypePWM(GPIO_PORTC_BASE, GPIO_PIN_4);

    //
    // Enable pin PB4 for PWM0 M0PWM2
    //
    MAP_GPIOPinConfigure(GPIO_PB4_M0PWM2);
    MAP_GPIOPinTypePWM(GPIO_PORTB_BASE, GPIO_PIN_4);

    //
    // Enable pin PD6 for PWM0 M0FAULT0
    //
    MAP_GPIOPinConfigure(GPIO_PD6_M0FAULT0);
    MAP_GPIOPinTypePWM(GPIO_PORTD_BASE, GPIO_PIN_6);

    //
    // Enable pin PC5 for PWM0 M0PWM7
    //
    MAP_GPIOPinConfigure(GPIO_PC5_M0PWM7);
    MAP_GPIOPinTypePWM(GPIO_PORTC_BASE, GPIO_PIN_5);

    //
    // Enable pin PB0 for USB0 USB0ID
    //
    MAP_GPIOPinTypeUSBAnalog(GPIO_PORTB_BASE, GPIO_PIN_0);

    //
    // Enable pin PC6 for USB0 USB0EPEN
    //
    MAP_GPIOPinConfigure(GPIO_PC6_USB0EPEN);
    MAP_GPIOPinTypeUSBDigital(GPIO_PORTC_BASE, GPIO_PIN_6);

    //
    // Enable pin PC7 for USB0 USB0PFLT
    //
    MAP_GPIOPinConfigure(GPIO_PC7_USB0PFLT);
    MAP_GPIOPinTypeUSBDigital(GPIO_PORTC_BASE, GPIO_PIN_7);

    //
    // Enable pin PD5 for USB0 USB0DP
    //
    MAP_GPIOPinTypeUSBAnalog(GPIO_PORTD_BASE, GPIO_PIN_5);

    //
    // Enable pin PB1 for USB0 USB0VBUS
    //
    MAP_GPIOPinTypeUSBAnalog(GPIO_PORTB_BASE, GPIO_PIN_1);

    //
    // Enable pin PD4 for USB0 USB0DM
    //
    MAP_GPIOPinTypeUSBAnalog(GPIO_PORTD_BASE, GPIO_PIN_4);
}

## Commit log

2015-12-30 initial mainboard import
    [I2C_LEVEL_SHIFT.sch, fan_tas_tic.kicad_pcb, fan_tas_tic.sch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]
2015-12-31 Added Input and output extension templates
    [InputExtension.kicad_pcb, InputExtension.sch, Mainboard.kicad_pcb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]
2016-01-04 Added the Input extension PCB layout
    [InputExtension.kicad_pcb, InputExtension.sch, Mainboard.kicad_pcb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]
2016-01-06 Made space for TM4C123 USB connector
    [fan_tas_tic.kicad_pcb, tiviaBoard.sch]
2016-01-13 Still Missing WS2811 level shifter
    [I2C_LEVEL_SHIFT.sch, fan_tas_tic.kicad_pcb, tiviaBoard.sch]
2016-01-16 Added 74HC04 buffer to WS2811 outputs
    [I2C_LEVEL_SHIFT.sch, fan_tas_tic.kicad_pcb, fan_tas_tic.sch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]
2016-01-17 Separated Tiva 5V from Power 5 V
    [I2C_LEVEL_SHIFT.sch, fan_tas_tic.kicad_pcb, fan_tas_tic.sch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]
2016-01-17 Larger pads and vias to allow some alignment error
    [fan_tas_tic.kicad_pcb, fan_tas_tic.sch, tiviaBoard.sch]
2016-01-17 Docu cosmetics
    [fan_tas_tic.csv]
2016-01-19 Cleaned up traces
    [fan_tas_tic.kicad_pcb, fan_tas_tic.sch, tiviaBoard.sch]
2016-02-28 Small documentation updates
    [fan_tas_tic.kicad_pcb, fan_tas_tic.sch, tiviaBoard.sch]
2016-06-12 Updated Schematic with minor changes after first prototype
    [I2C_LEVEL_SHIFT.sch, fan_tas_tic.kicad_pcb, fan_tas_tic.sch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]
2016-06-25 Started to work on Rev2
    [powerRails.sch]
2016-06-26 Made I2C level converters more neat
    [I2C_LEVEL_SHIFT.sch, fan_tas_tic.kicad_pcb, fan_tas_tic.sch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]
2018-11-14 Output extension looks good. Diodes still missing
    [OutputExtension.kicad_pcb, OutputExtension.sch, powerChannel.sch]
2018-11-14 Add diodes
    [OutputExtension.kicad_pcb, OutputExtension.sch, powerChannel.sch]
2018-11-14 Output extension ready for fab
    [OutputExtension.kicad_pcb, OutputExtension.sch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]
2018-11-14 .4 mm traces
    [OutputExtension.kicad_pcb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]
2018-11-16 Fabbed version
    [OutputExtension.kicad_pcb, OutputExtension.sch, powerChannel.sch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]
2018-12-14 Input extension 2
    [InputExtension.kicad_pcb, InputExtension.sch]
2018-12-14 Add new input extension pcb
    [InputExtension.kicad_pcb, InputExtension.sch]
2018-12-17 Output extension: chunkier freewheelingdiode
    [OutputExtension.kicad_pcb, OutputExtension.sch, powerChannel.sch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]
